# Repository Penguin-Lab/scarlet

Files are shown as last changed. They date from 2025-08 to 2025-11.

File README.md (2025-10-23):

# scarlet
A Scarlet é uma hexapod desenvolvida na disciplina de Robôs a Patas para andar de forma autônoma ou para ser controlada pelo celular. Para se locomover, ela possui 6 patas de 3 graus de liberdade cada (3 motores) e uma ESP32 que comanda o conjunto! Ela é a nossa viúva negra, a irmã da Tiffany e a nova integrante robótica do nosso espaço inteligente!

# Estrutura física
A estrutura física do robô é composta por seis patas de três eixos cada (três motores). As patas são fixadas a duas placas de PLA para deixar o robô firme. As peças são todas projetadas em 3D e foram impressas utilizando PLA, podendo ser encontradas na pasta Pecas_3d deste projeto.

   

## Peças 3D em STL
As peças em 3D desenvolvidas para este projeto foram baseadas no projeto da hexapod Tiffany. Na pasta Pecas_3d, estão listadas essas peças em STL. Para ajudar, segue abaixo uma lista de todas as peças que devem ser impressas e qual o valor da sua maior dimensão (para ajudar na escolha da impressora):
* Corpo
  * 1x [SCARLET_BODY_DOWN.STL (230 mm)](https://github.com/Penguin-Lab/scarlet/blob/main/Pecas_3d/SCARLET_BODY_DOWN.STL)
  * 1x [SCARLET_BODY_UP.STL (230 mm)](https://github.com/Penguin-Lab/scarlet/blob/main/Pecas_3d/SCARLET_BODY_UP.STL)
  * 4x [SCARLET_SPACER.STL (68 mm)](https://github.com/Penguin-Lab/scarlet/blob/main/Pecas_3d/SCARLET_SPACER.STL)
  * 2x [SCARLET_SPACER_FRONT.STL (68 mm)](https://github.com/Penguin-Lab/scarlet/blob/main/Pecas_3d/SCARLET_SPACER_FRONT.STL)
  * 1x [SCARLET_SUPPORT_PCI.STL (120 mm)](https://github.com/Penguin-Lab/scarlet/blob/main/Pecas_3d/SCARLET_SUPPORT_PCI.STL)
  * 1x [SCARLET_SUPPORT_SWITCH.STL (50 mm)](https://github.com/Penguin-Lab/scarlet/blob/main/Pecas_3d/SCARLET_SUPPORT_SWITCH.STL)
  * 1x [SCARLET_SYMBOL.STL (50 mm)](https://github.com/Penguin-Lab/scarlet/blob/main/Pecas_3d/SCARLET_SYMBOL.STL)
  * 1x [SCARLET_LOGO.STL (50 mm)](https://github.com/Penguin-Lab/scarlet/blob/main/Pecas_3d/SCARLET_LOGO.STL)
* Patas
  * 6x [SCARLET_TIBIA_LEFT.STL (141 mm)](https://github.com/Penguin-Lab/scarlet/blob/main/Pecas_3d/SCARLET_TIBIA_LEFT.STL)
  * 6x [SCARLET_TIBIA_LEFT.STL espelhado (141 mm)](https://github.com/Penguin-Lab/scarlet/blob/main/Pecas_3d/SCARLET_TIBIA_LEFT.STL)
  * 6x [SCARLET_TIBIA_MIDDLE.STL (63 mm)](https://github.com/Penguin-Lab/scarlet/blob/main/Pecas_3d/SCARLET_TIBIA_MIDDLE.STL)
  * 3x [SCARLET_SHIELD_A.STL (10 mm)](https://github.com/Penguin-Lab/scarlet/blob/main/Pecas_3d/SCARLET_SHIELD_A.STL)
  * 3x [SCARLET_SHIELD_A.STL espelhado (10 mm)](https://github.com/Penguin-Lab/scarlet/blob/main/Pecas_3d/SCARLET_SHIELD_A.STL)
  * 3x [SCARLET_SHIELD_B.STL (10 mm)](https://github.com/Penguin-Lab/scarlet/blob/main/Pecas_3d/SCARLET_SHIELD_B.STL)
  * 3x [SCARLET_SHIELD_B.STL espelhado (10 mm)](https://github.com/Penguin-Lab/scarlet/blob/main/Pecas_3d/SCARLET_SHIELD_B.STL)
  * 3x [SCARLET_FEMUR_FRONT.STL (110 mm)](https://github.com/Penguin-Lab/scarlet/blob/main/Pecas_3d/SCARLET_FEMUR_FRONT.STL)
  * 3x [SCARLET_FEMUR_BACK.STL (118 mm)](https://github.com/Penguin-Lab/scarlet/blob/main/Pecas_3d/SCARLET_FEMUR_BACK.STL)
  * 3x [SCARLET_FEMUR_FRONT.STL espelhado (110 mm)](https://github.com/Penguin-Lab/scarlet/blob/main/Pecas_3d/SCARLET_FEMUR_FRONT.STL)
  * 3x [SCARLET_FEMUR_BACK.STL espelhado (118 mm)](https://github.com/Penguin-Lab/scarlet/blob/main/Pecas_3d/SCARLET_FEMUR_BACK.STL)
  * 6x [SCARLET_FEMUR_MIDDLE.STL (51 mm)](https://github.com/Penguin-Lab/scarlet/blob/main/Pecas_3d/SCARLET_FEMUR_MIDDLE.STL)
  * 6x [SCARLET_OMBRO_UP.STL (61 mm)](https://github.com/Penguin-Lab/scarlet/blob/main/Pecas_3d/SCARLET_OMBRO_UP.STL)
  * 3x [SCARLET_OMBRO_DOWN_LEFT.STL (61 mm)](https://github.com/Penguin-Lab/scarlet/blob/main/Pecas_3d/SCARLET_OMBRO_DOWN_LEFT.STL)
  * 3x [SCARLET_OMBRO_DOWN_LEFT.STL espelhado (61 mm)](https://github.com/Penguin-Lab/scarlet/blob/main/Pecas_3d/SCARLET_OMBRO_DOWN_LEFT.STL)
* Motor
  * 12x [SCARLET_TAMPA_MOTOR_DS3230.STL (41 mm)](https://github.com/Penguin-Lab/scarlet/blob/main/Pecas_3d/SCARLET_TAMPA_MOTOR_DS3230.STL)

Obs 1: a tampa de 12 motores deverão ser trocadas pelas peças [SCARLET_TAMPA_MOTOR_DS3230.STL](https://github.com/Penguin-Lab/scarlet/blob/main/Pecas_3d/SCARLET_TAMPA_MOTOR_DS3230.STL) para que seja possível fixar os rolamentos nas patas. Serão utilizados 3 rolamentos por pata.

Obs 2: os motores ficam fixados nas peças por [discos metálicos pequenos padrão para eixos de servo](https://a.aliexpress.com/_mPHt3nf).



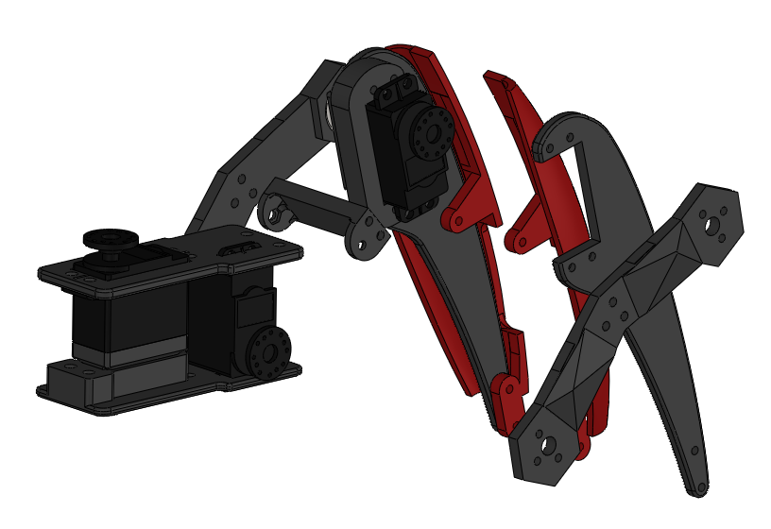
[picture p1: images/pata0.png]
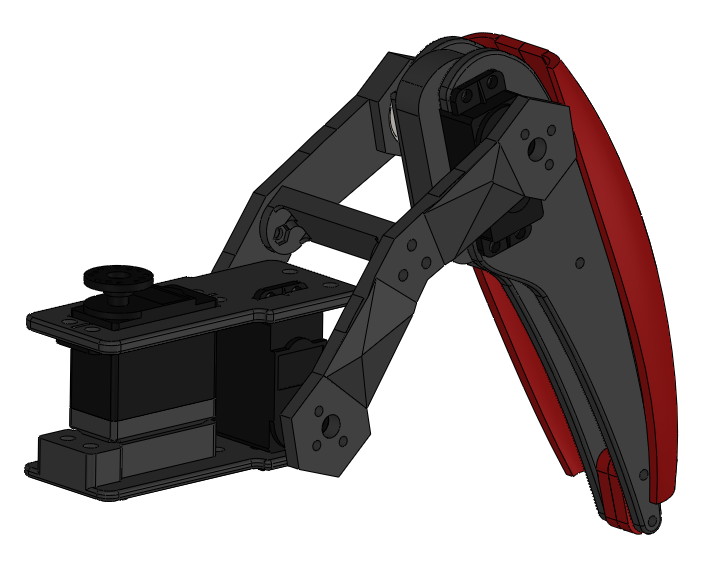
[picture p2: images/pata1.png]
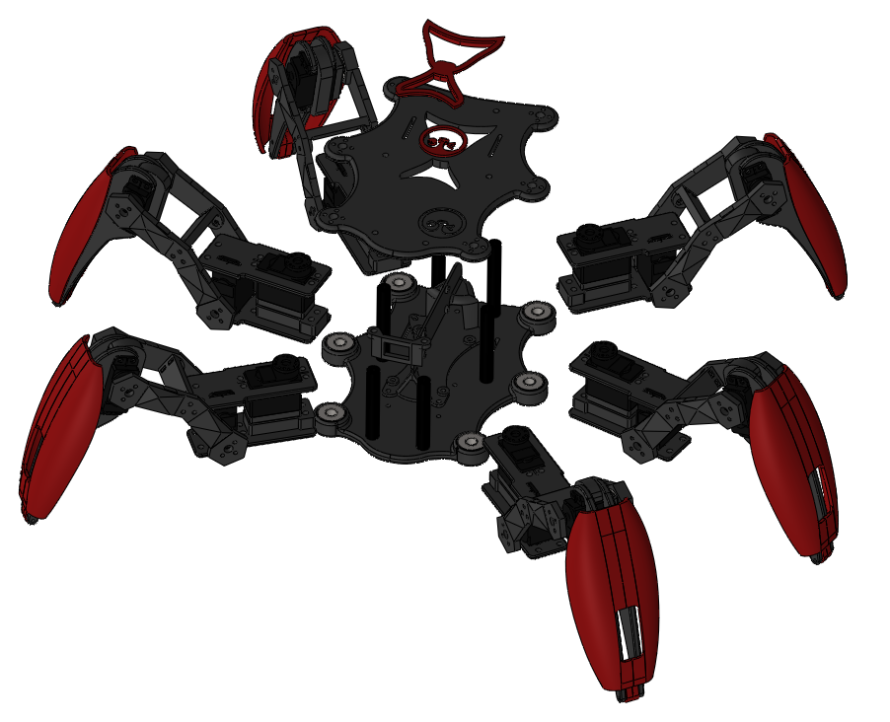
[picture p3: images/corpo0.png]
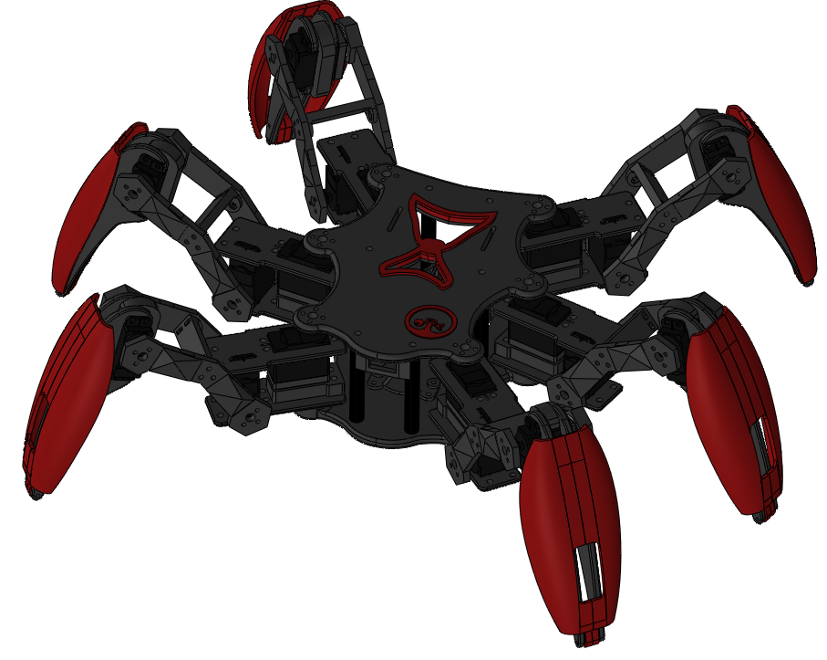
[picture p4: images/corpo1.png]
   

## Outros itens da estrutura
Alguns outros itens são necessários para finalizar a estrutura da Tiffany:
* 6x Parafusos m4 ou similar de cm, arruelas e porcas auto-travantes: prender as peças [SCARLET_BODY_UP.STL](https://github.com/Penguin-Lab/scarlet/blob/main/Pecas_3d/SCARLET_BODY_UP.STL) e [SCARLET_BODY_DOWN.STL](https://github.com/Penguin-Lab/scarlet/blob/main/Pecas_3d/SCARLET_BODY_DOWN.STL)
* 12x Parafusos m4 de 5 cm: prender as peças [SCARLET_OMBRO_DOWN_LEFT.STL](https://github.com/Penguin-Lab/scarlet/blob/main/Pecas_3d/SCARLET_OMBRO_DOWN_LEFT.STL) e [SCARLET_OMBRO_UP.STL](https://github.com/Penguin-Lab/scarlet/blob/main/Pecas_3d/SCARLET_OMBRO_UP.STL)
* 24x Parafusos m4 de 5,5 cm: prender as peças [SCARLET_OMBRO_DOWN_LEFT.STL](https://github.com/Penguin-Lab/scarlet/blob/main/Pecas_3d/SCARLET_OMBRO_DOWN_LEFT.STL) e [SCARLET_OMBRO_UP.STL](https://github.com/Penguin-Lab/scarlet/blob/main/Pecas_3d/SCARLET_OMBRO_UP.STL)
* Parafusos m3 de cm: prender todas as peças das patas e a [SCARLET_SUPORT_PCI.STL](https://github.com/Penguin-Lab/scarlet/blob/main/Pecas_3d/SCARLET_SUPORT_PCI.STL) no corpo do robô e na placa
* 6x Tiras de EVA de 5mm: colar e prender com braçadeira na ponta das peças [SCARLET_SHIELD_A.STL](https://github.com/Penguin-Lab/scarlet/blob/main/Pecas_3d/SCARLET_SHIELD_A.STL) e [SCARLET_SHIELD_B.STL](https://github.com/Penguin-Lab/scarlet/blob/main/Pecas_3d/SCARLET_SHIELD_B.STL) para evitar que o robô deslize

## Placa de circuito impresso
No projeto, foi desenvolvida uma placa de circuito para servir como shield para a ESP32 e conexão com as duas placas PCA9685 e com futuros sensores e displays I2C.

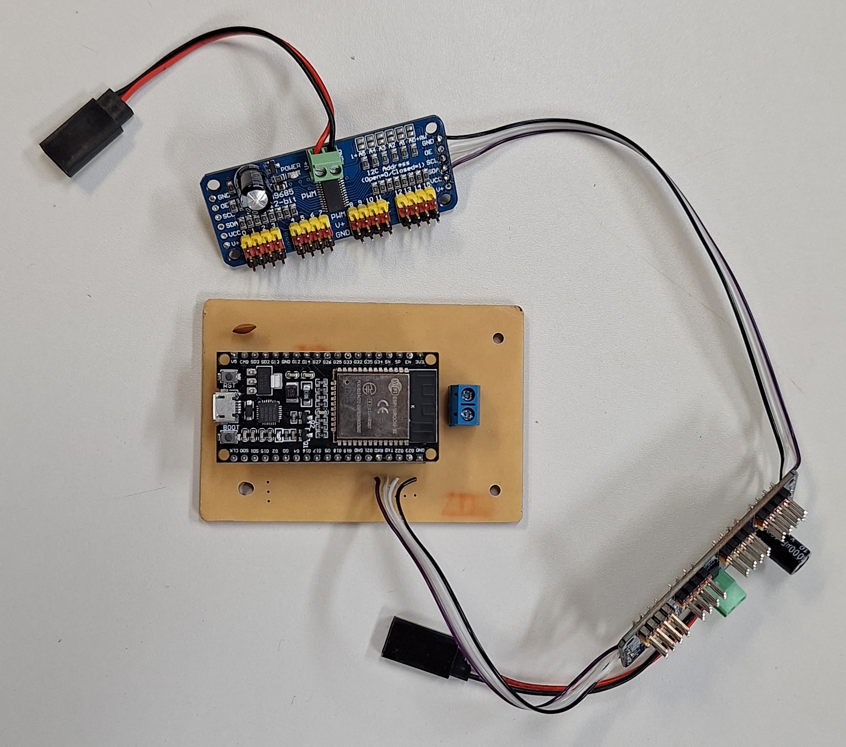
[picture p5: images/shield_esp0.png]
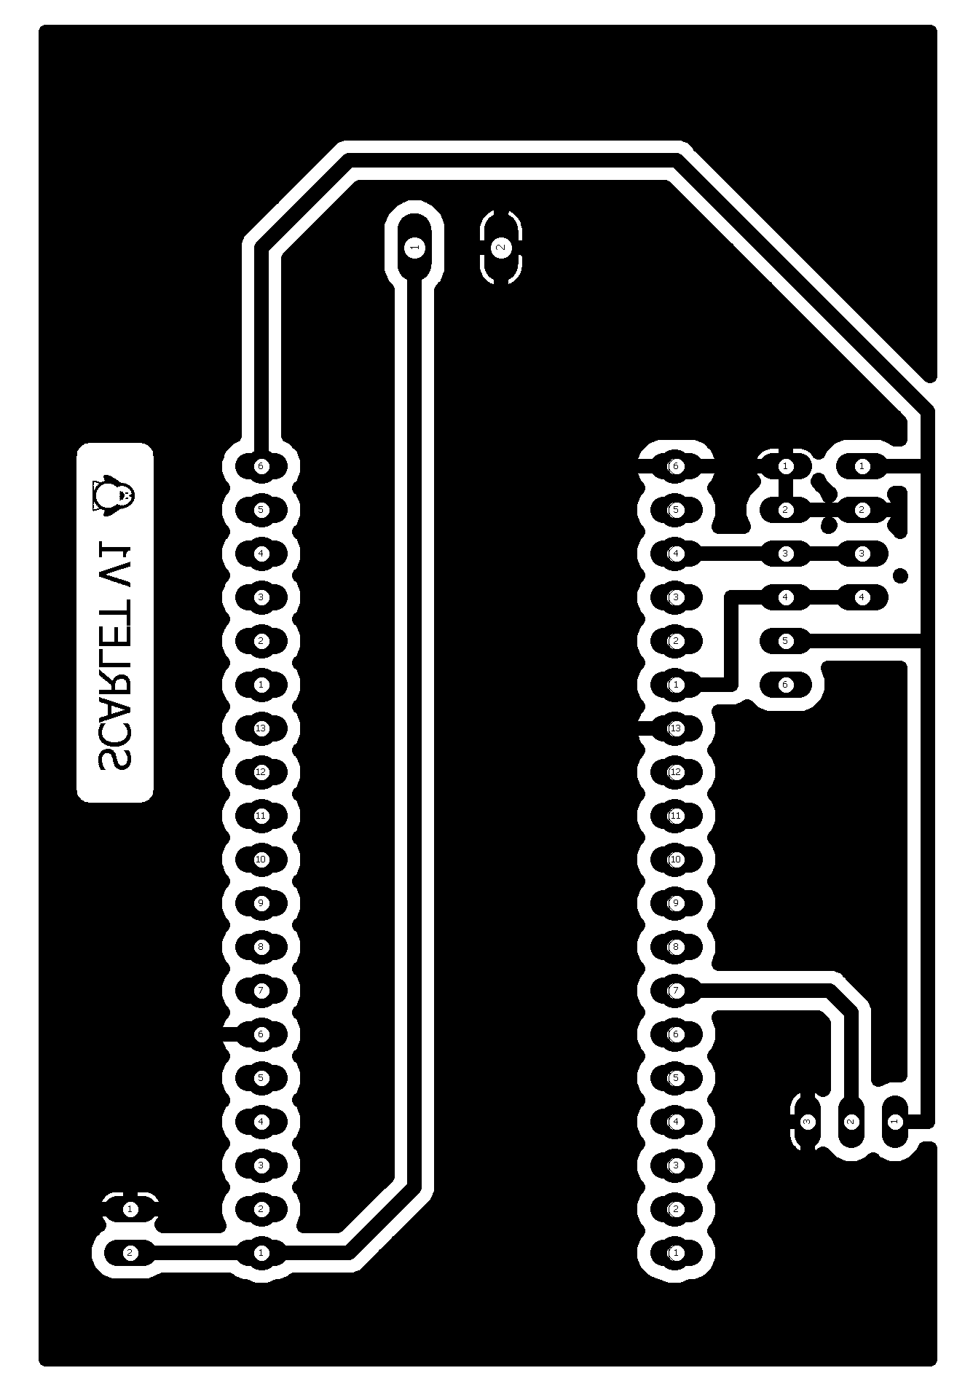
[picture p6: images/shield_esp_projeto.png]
    

## Calibração dos motores
A calibração dos motores é feita utilizando o [CALIBRADOR DE MOTORES](https://github.com/Penguin-Lab/calib_servomotor) conectado às PCAs da Scarlet. Isso deve ser feito pelo clock das PCAs ser diferente de uma placa para outra. Logo, os motores da esquerda são calibrados utilizando a PCA da esquerda e os da direita com a PCA da direita. Os valores retornados pela calibração são jogados nesta [PLANILHA](https://docs.google.com/spreadsheets/d/1Kh9AVbb79lXnJq5dlCiB7NEVVmcJWRX6X2CdDR9_QZo/edit?usp=sharing). A planilha ajeita os valores de PWM retornados na IDE do Arduino para valores que representem 0 e 180 graus dos motores já na estrutura das patas. Esses valores são os mesmos listados no código de comando da Scarlet.

## Componentes eletrônicos
Os componentes eletrônicos embarcados no robô e equipamentos utilizados são:
* Controlador com Wi-fi e Bluetooth
  * 1x ESP32 (38 pinos)
* Motores
  * 18x Servo DS3230 PRO-180
* 2x Placas PCA9685 para comando dos 18 motores
* Chave (switch)
* Alimentação
  * Bateria Zippy LiFe 1100mAh 2s 6,6V (ESP32)
  * Bateria TM Hobbies LiFe 2100mAh 2s 6,6v (motores)

# Software
Na pasta de códigos, há um código de programação da ESP32 (38 pinos). Ele é um exemplo em C++ do comando de movimentação da Tiffany:
* Dabble: a ESP32 pode se comunicar com o aplicativo Dabble no celular e receber comandos de ação.

## Alunos participantes e desenvolvedores da Scarlet
* Állefe Amorim Florindo
* Eduarda Ferreira Cipriano
* Gustavo Assis Ferreira
* Joab Felippe de Souza Lima
* João Pedro Queiroz dos Santos
* Junior Guimarães de Oliveira
* Luis Philipe Zioto de Barros
* Rafaela da Silva Crise
* Ricardo dos Santos Barros
* Samuel Gurgel Rocha

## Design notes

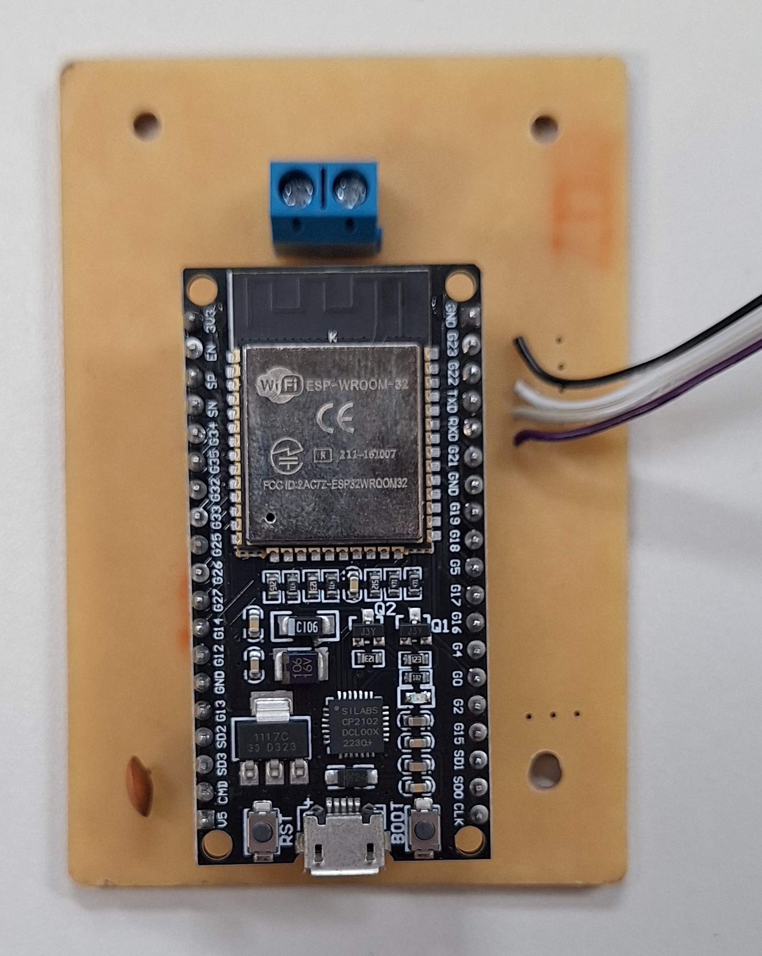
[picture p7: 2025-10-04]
images/shield_esp1.png

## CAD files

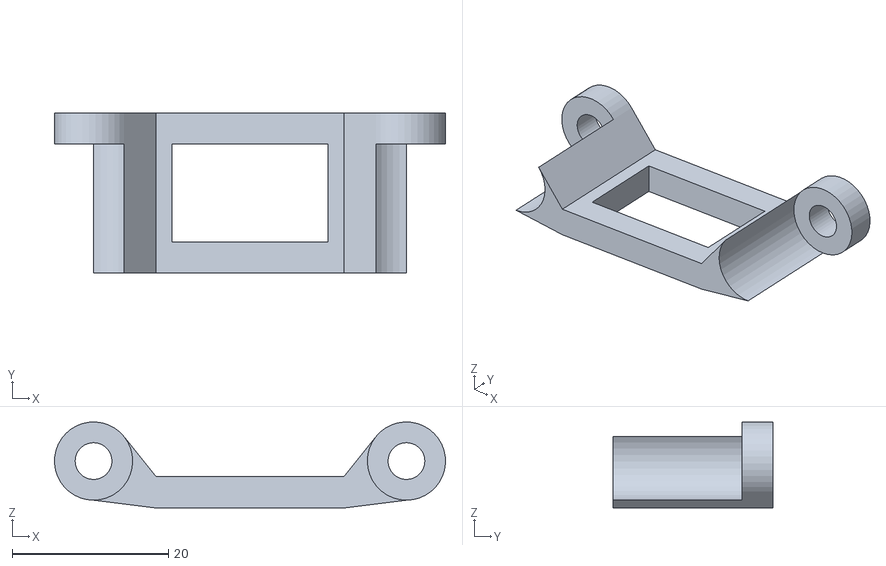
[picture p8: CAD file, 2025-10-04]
Pecas_3d/SCARLET_SUPORT_SWITCH.STL
50.0 x 20.5 x 11.0

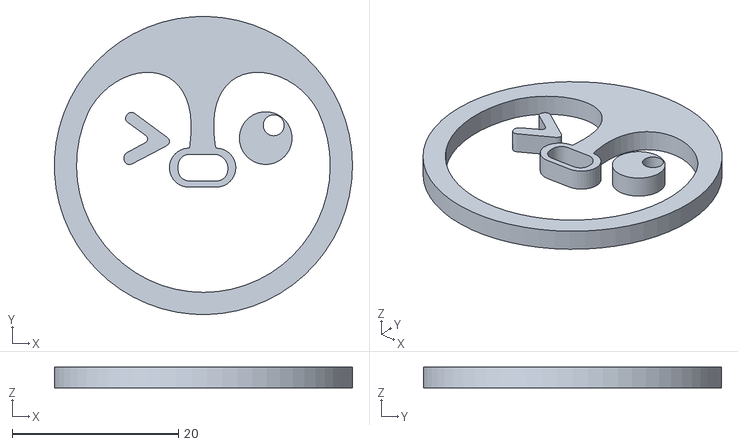
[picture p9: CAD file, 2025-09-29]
Pecas_3d/SCARLET_LOGO.STL
35.9 x 35.9 x 2.50

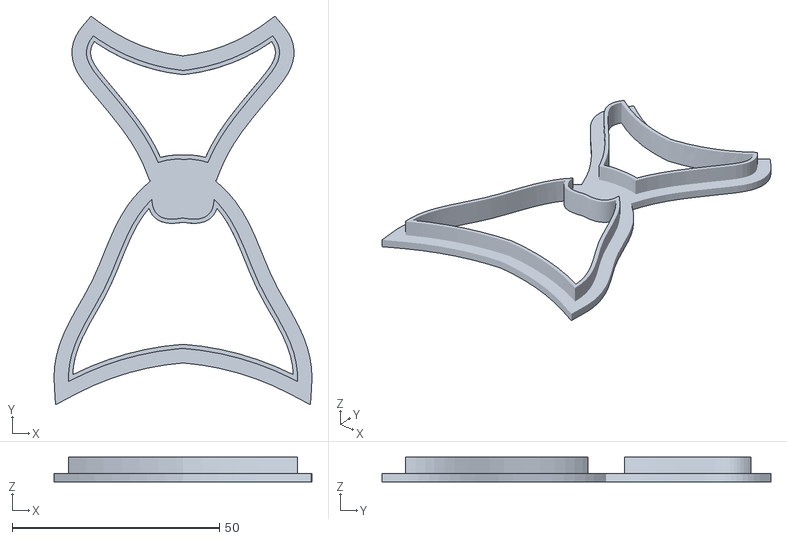
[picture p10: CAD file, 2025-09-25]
Pecas_3d/SCARLET_SYMBOL.STL
62.2 x 93.7 x 6.00

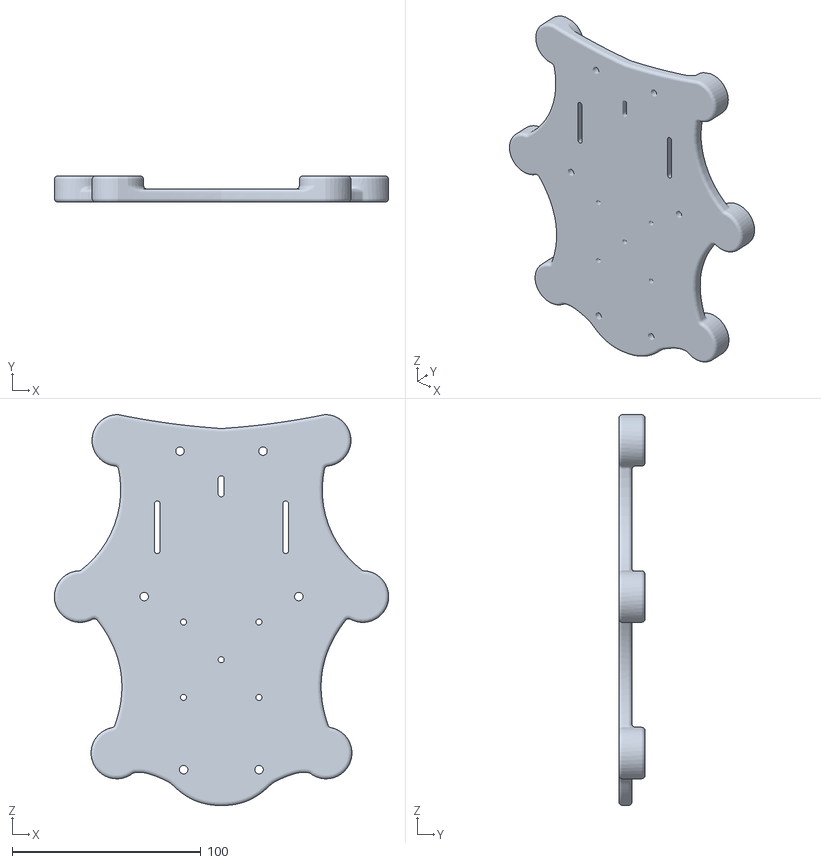
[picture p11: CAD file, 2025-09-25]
Pecas_3d/SCARLET_BODY_DOWN.STL
177.4 x 14.0 x 207.4

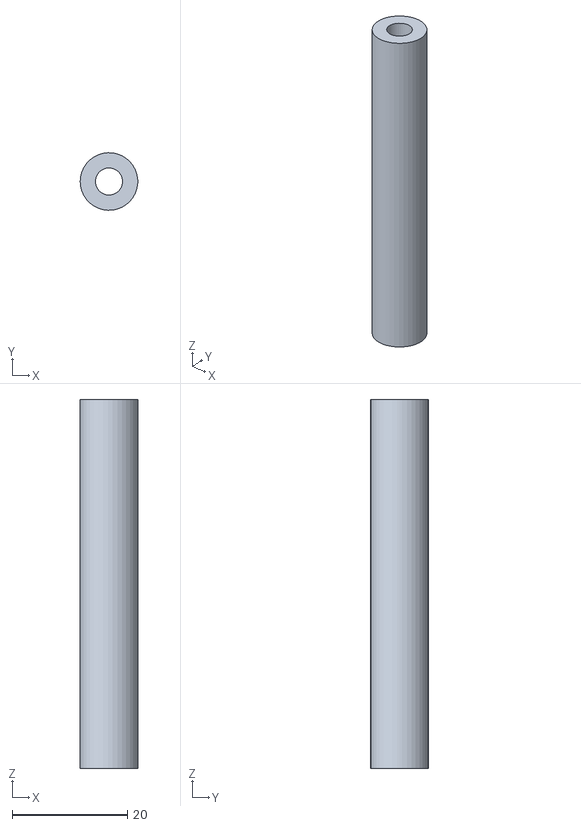
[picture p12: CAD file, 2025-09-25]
Pecas_3d/SCARLET_SPACER_FRONT.STL
10.0 x 9.99 x 64.0

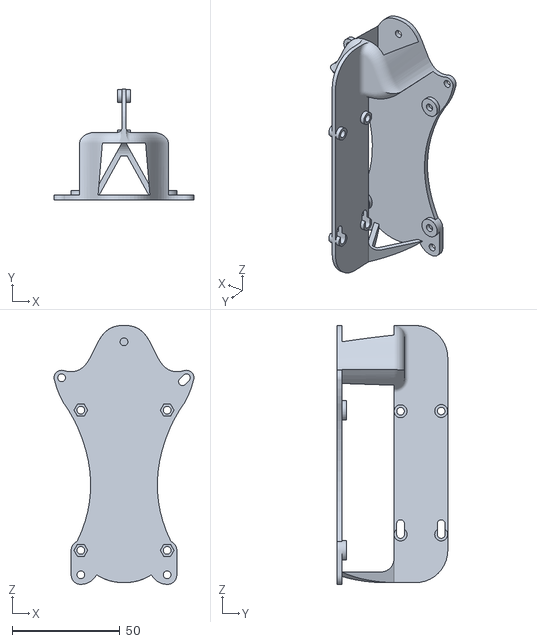
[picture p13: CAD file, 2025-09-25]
Pecas_3d/SCARLET_SUPORT_PCI.STL
64.8 x 51.3 x 120.1

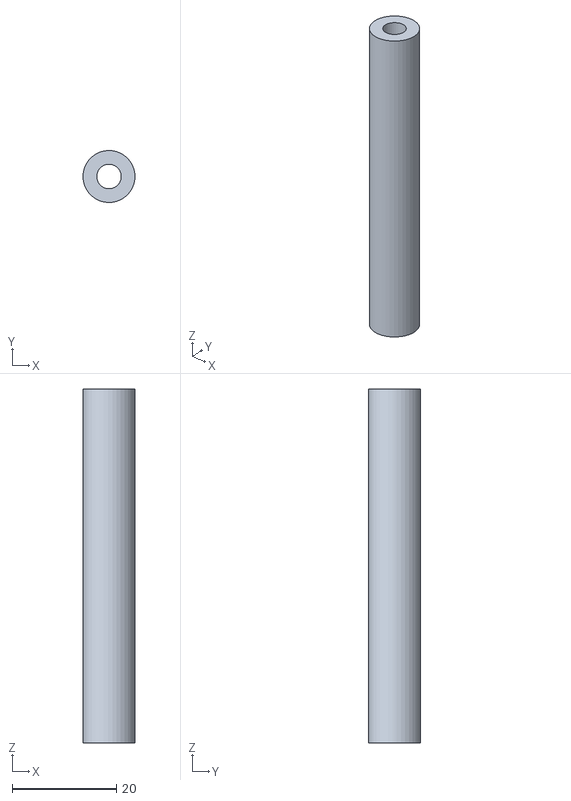
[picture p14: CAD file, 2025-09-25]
Pecas_3d/SCARLET_SPACER.STL
10.0 x 9.99 x 68.0

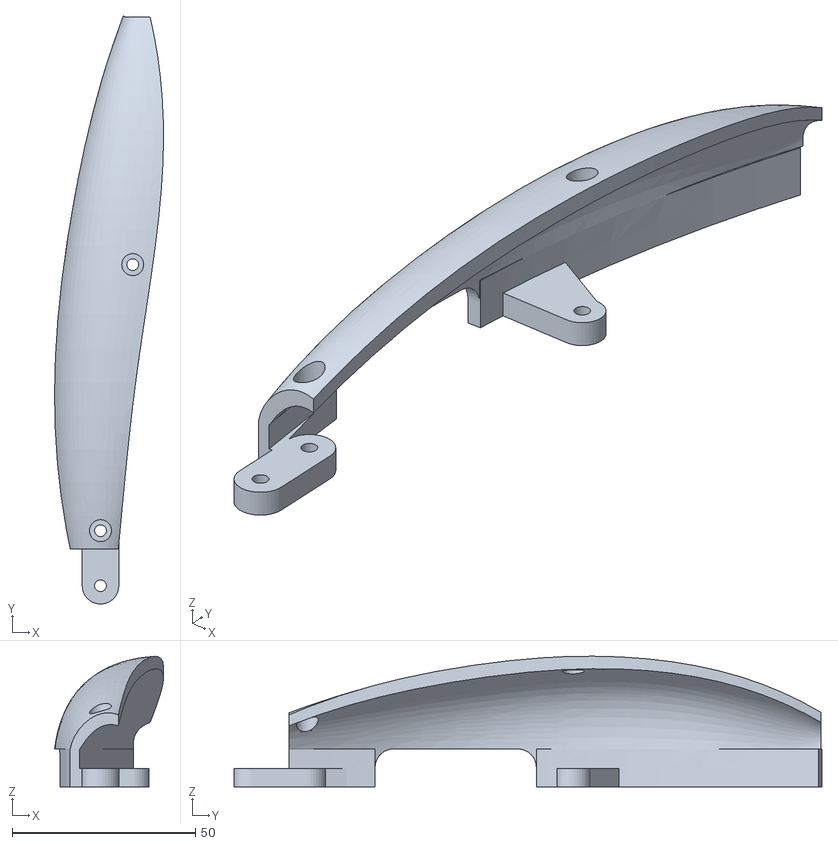
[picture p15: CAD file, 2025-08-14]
Pecas_3d/SCARLET_SHIELD_A.STL
29.7 x 160.2 x 35.6

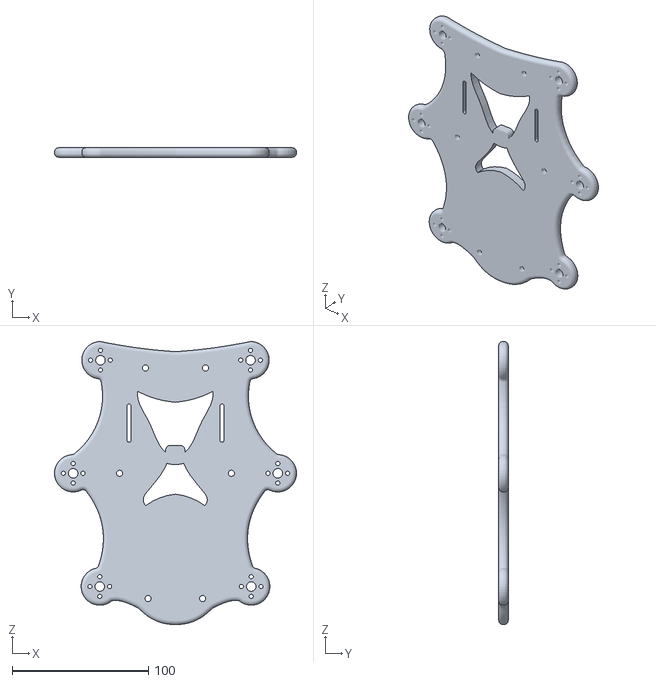
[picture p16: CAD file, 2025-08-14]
Pecas_3d/SCARLET_BODY_UP.STL
177.4 x 7.00 x 207.4

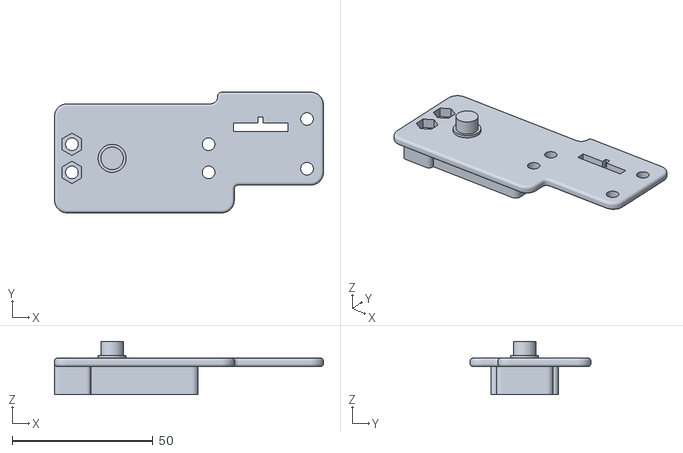
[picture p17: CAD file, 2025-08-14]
Pecas_3d/SCARLET_OMBRO_DOWN_LEFT.STL
95.7 x 43.0 x 19.0

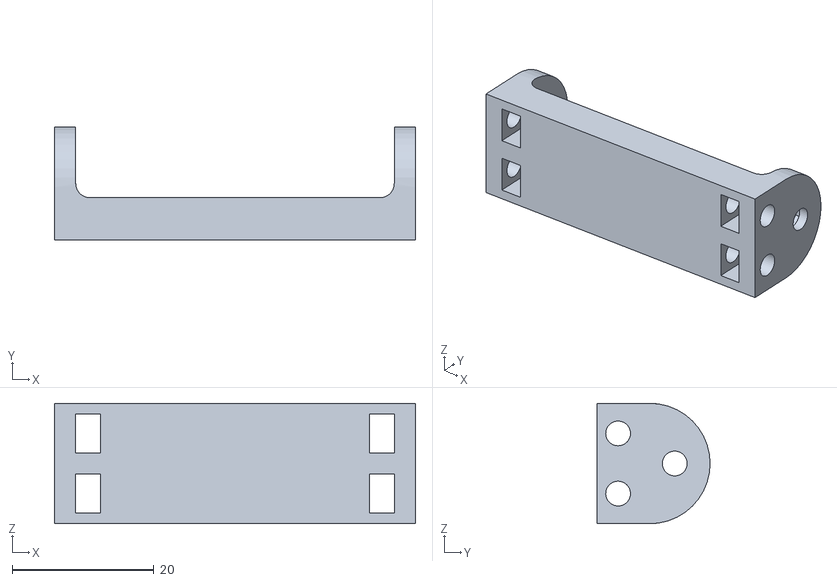
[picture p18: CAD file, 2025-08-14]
Pecas_3d/SCARLET_FEMUR_MIDDLE.STL
51.0 x 16.0 x 17.0

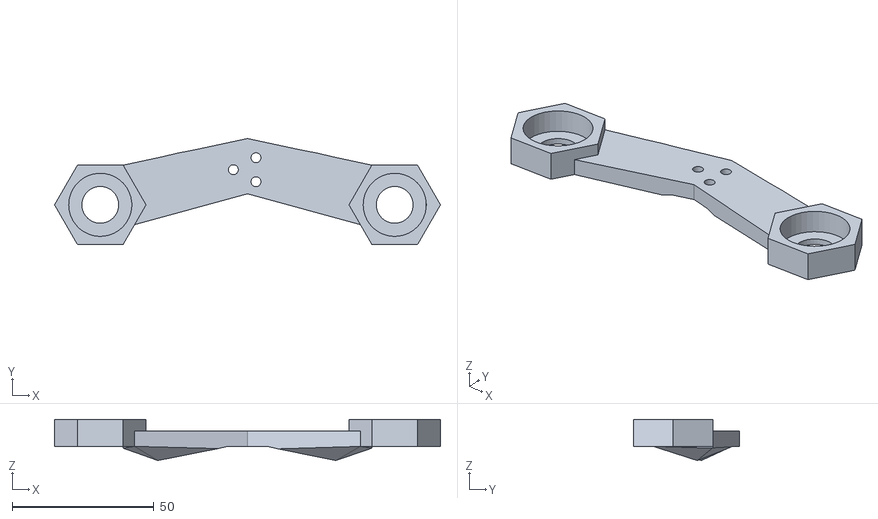
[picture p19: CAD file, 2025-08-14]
Pecas_3d/SCARLET_FEMUR_BACK.STL
136.3 x 37.4 x 14.5

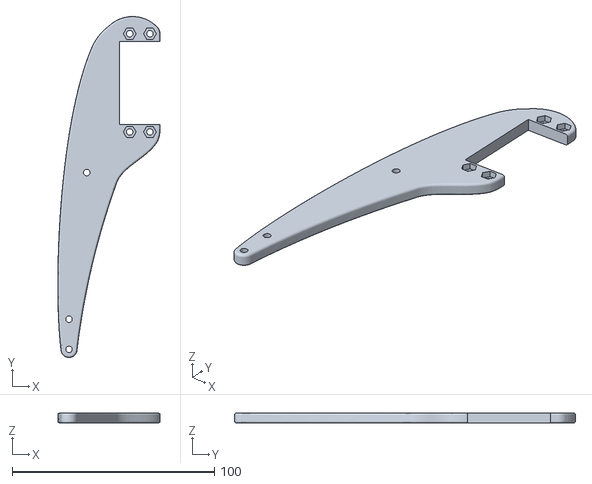
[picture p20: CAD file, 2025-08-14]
Pecas_3d/SCARLET_TIBIA_LEFT.STL
50.7 x 168.7 x 5.00

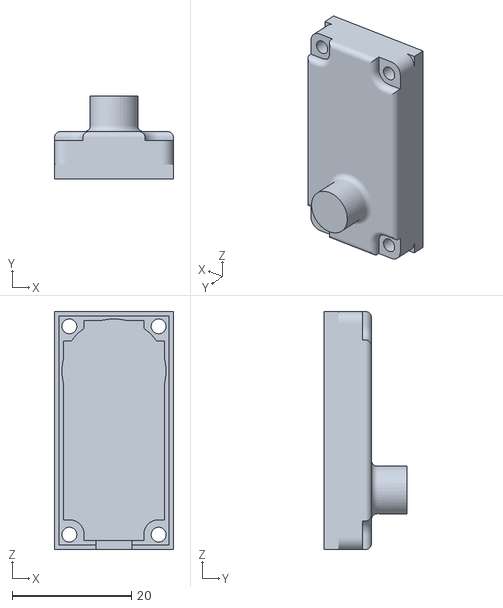
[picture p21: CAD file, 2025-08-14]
Pecas_3d/SCARLET_TAMPA_MOTOR_DS3230.STL
20.0 x 14.0 x 40.0

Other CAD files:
Pecas_3d/SCARLET_SHIELD_B.STL
Pecas_3d/SCARLET_FEMUR_FRONT.STL
Pecas_3d/SCARLET_OMBRO_UP.STL
Pecas_3d/SCARLET_TIBIA_MIDDLE.STL

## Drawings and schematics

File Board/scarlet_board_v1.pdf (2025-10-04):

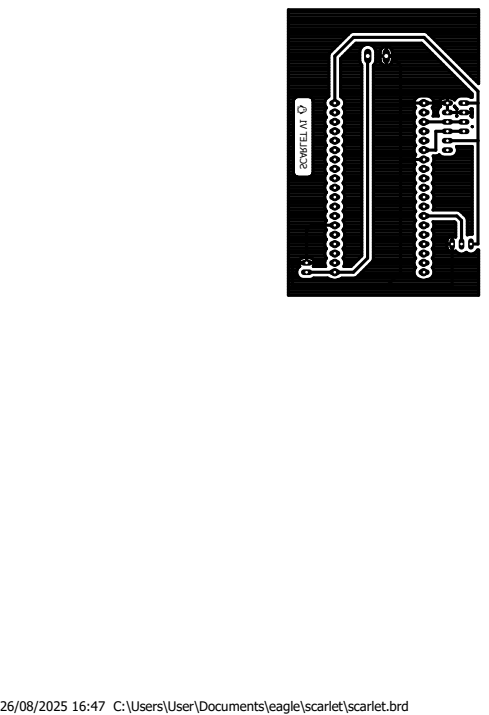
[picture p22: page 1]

26/08/2025 16:47 C:\Users\User\Documents\eagle\scarlet\scarlet.brd SCARLET V1

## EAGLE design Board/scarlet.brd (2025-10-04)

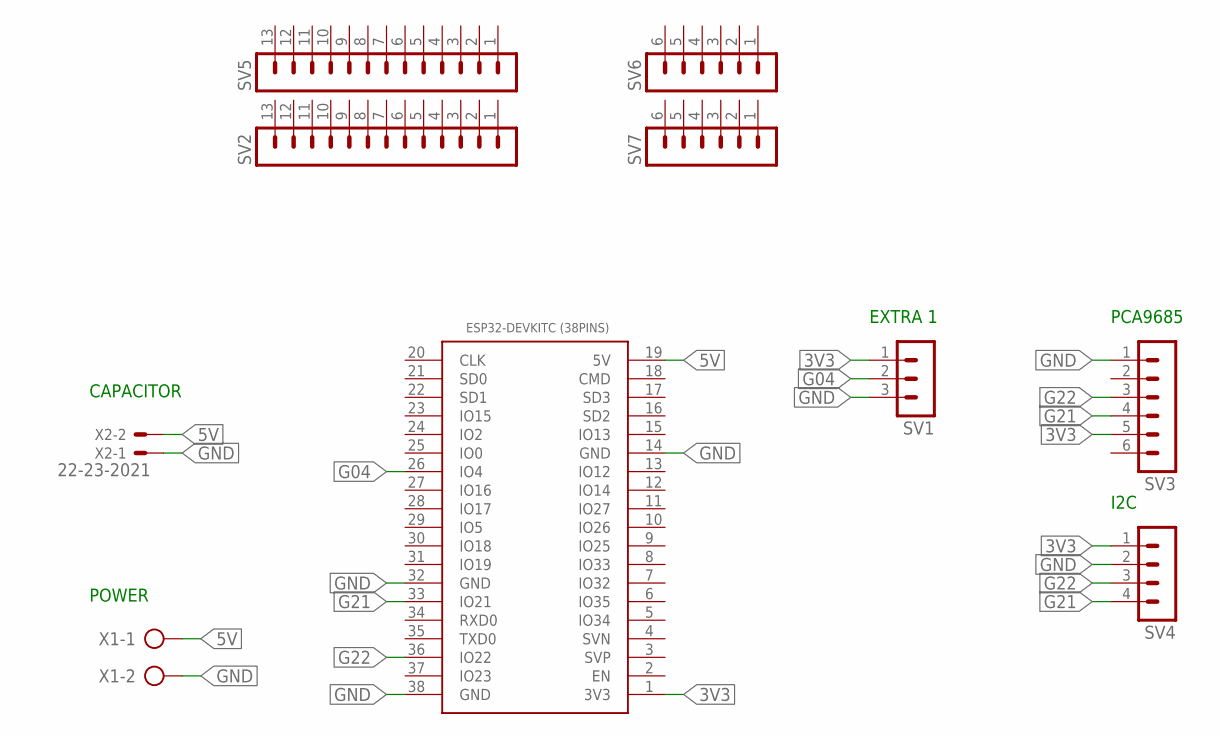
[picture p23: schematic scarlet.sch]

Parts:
ESP32-DEVKITC(38PINS)1: ESP32DEVKITC_38PINS; ESP32-DEVKITC
SV1: MA03-1
SV2, SV5: MA13-1
SV3, SV6, SV7: MA06-1
SV4: MA04-1
X1: AK300/2
X2: 22-23-2021

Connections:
3V3: ESP32-DEVKITC(38PINS)1.1 (3V3), SV1.1, SV3.5, SV4.1
5V: ESP32-DEVKITC(38PINS)1.19 (5V), X1.1, X2.2
G04: ESP32-DEVKITC(38PINS)1.26 (IO4), SV1.2
G21: ESP32-DEVKITC(38PINS)1.33 (IO21), SV3.4, SV4.4
G22: ESP32-DEVKITC(38PINS)1.36 (IO22), SV3.3, SV4.3
GND: ESP32-DEVKITC(38PINS)1.14 (GND), ESP32-DEVKITC(38PINS)1.32 (GND), ESP32-DEVKITC(38PINS)1.38 (GND), SV1.3, SV3.1, SV4.2, X1.2, X2.1

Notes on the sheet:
CAPACITOR
POWER
EXTRA 1
PCA9685
I2C

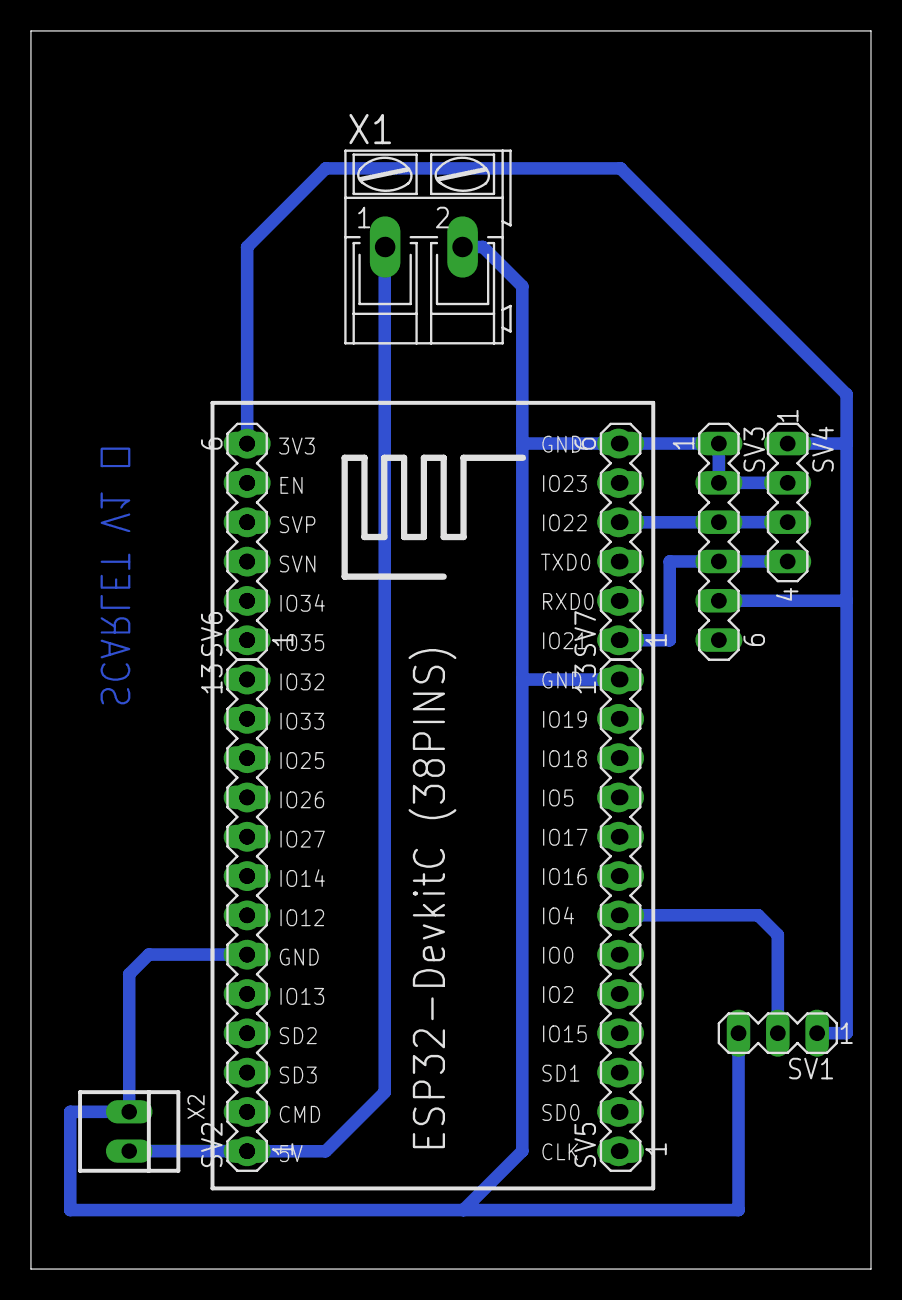
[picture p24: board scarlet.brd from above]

Board: 2 copper layers, 54.3 x 80.0 mm, 10 parts (0 on the bottom side), 6 nets.

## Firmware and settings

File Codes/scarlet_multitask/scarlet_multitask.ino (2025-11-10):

#define CUSTOM_SETTINGS
#define INCLUDE_GAMEPAD_MODULE
#include <DabbleESP32.h>
#include <Wire.h>
#include <Adafruit_PWMServoDriver.h>
#include <math.h>

#define TOTAL_PONTOS 25
#define METADE_PONTOS TOTAL_PONTOS / 2
#define TOTAL_PONTOS_CIRCULAR 25
#define DEBUG_SIMULADOR false

int OFFSET_ESQF = 0;
int OFFSET_DIRT = METADE_PONTOS;
int OFFSET_ESQM = METADE_PONTOS;
int OFFSET_DIRF = METADE_PONTOS;
int OFFSET_ESQT = 0;
int OFFSET_DIRM = 0;

Adafruit_PWMServoDriver pwmE = Adafruit_PWMServoDriver(0x40);
Adafruit_PWMServoDriver pwmD = Adafruit_PWMServoDriver(0x41);

struct int3 {
    int ombro, femur, tibia;

    // Soma
    int3 operator+(const int3& rhs) const {
      return { ombro + rhs.ombro, femur + rhs.femur, tibia + rhs.tibia };
    }

    // Subtracao
    int3 operator-(const int3& rhs) const {
      return { ombro - rhs.ombro, femur - rhs.femur, tibia - rhs.tibia };
    }

    // Multiplicacao por escalar
    int3 operator*(int scalar) const {
      return { ombro * scalar, femur * scalar, tibia * scalar };
    }

    // Divisao por escalar
    int3 operator/(int scalar) const {
      return { ombro / scalar, femur / scalar, tibia / scalar };
    }
};

struct float3 {
    float ombro, femur, tibia;

    // Soma
    float3 operator+(const float3& rhs) const {
      return { ombro + rhs.ombro, femur + rhs.femur, tibia + rhs.tibia };
    }

    // Subtracao
    float3 operator-(const float3& rhs) const {
      return { ombro - rhs.ombro, femur - rhs.femur, tibia - rhs.tibia };
    }

    // Multiplicacao por escalar
    float3 operator*(float scalar) const {
      return { ombro * scalar, femur * scalar, tibia * scalar };
    }

    // Divisao por escalar
    float3 operator/(float scalar) const {
      return { ombro / scalar, femur / scalar, tibia / scalar };
    }
};

int3 radToDegree(float3 angles_rad){
    return {int(angles_rad.ombro * 180.0 / M_PI),int(angles_rad.femur * 180.0 / M_PI),int(angles_rad.tibia * 180.0 / M_PI)};
}

float3 degreeToRad(int3 angles){
    return {float(angles.ombro) * M_PI / 180.0,float(angles.femur) * M_PI / 180.0,float(angles.tibia) * M_PI / 180.0};
}

struct floatxyz {
    float x, y, z;

    // Soma
    floatxyz operator+(const floatxyz& rhs) const {
      return { x + rhs.x, y + rhs.y, z + rhs.z };
    }

    // Subtracao
    floatxyz operator-(const floatxyz& rhs) const {
      return { x - rhs.x, y - rhs.y, z - rhs.z };
    }

    // Multiplicacao por escalar
    floatxyz operator*(float scalar) const {
      return { x * scalar, y * scalar, z * scalar };
    }

    // Divisao por escalar
    floatxyz operator/(float scalar) const {
      return { x / scalar, y / scalar, z / scalar };
    }

    floatxyz operator*(const floatxyz& rhs) const {
      return { x * rhs.x, y * rhs.y, z * rhs.z };
    }
};

float joystickToRad(int joystickAngle){
  float angle_rad = (float(joystickAngle)-90.0)*M_PI/180.0;
  while (angle_rad > M_PI) angle_rad -= 2*M_PI;
  while (angle_rad < -M_PI) angle_rad += 2*M_PI;
  
  return angle_rad;
}

int joystickToInt(int joystickAngle, int deltaAngle){
  int angle = joystickAngle-90;
  while (angle > 180) angle -= 360;
  while (angle < -180) angle += 360;
  // Verifica faixas e "trava" no valor mais proximo
  if (abs(angle - 180) <= deltaAngle || abs(angle + 180) <= deltaAngle){
    return 180;
  }
  else if (abs(angle - 90) <= deltaAngle){
    return 90;
  }
  else if (abs(angle + 90) <= deltaAngle){
    return -90;
  }
  else if (abs(angle) <= deltaAngle){
    return 0;
  }
  return angle;
}
struct Pata {
  Adafruit_PWMServoDriver* pwm;
  int3 pins;
  int3 angles;
  floatxyz xyz_ini;
  int3 LIMMIN;
  int3 LIMMAX;
  float L1, L2, L3;
  float P0[2], P1[2], P2[2], P3[2];

  Pata(Adafruit_PWMServoDriver* pwm, int pinOmbro, int pinFemur, int pinTibia, int OMIN, int OMAX, int FMIN, int FMAX, int TMIN, int TMAX) {
    this->pwm = pwm;
    this->pins = {pinOmbro,pinFemur,pinTibia};
    this->angles = {-1,-1,-1};
    this->xyz_ini = {0.0f,0.0f,0.0f};
    this->LIMMIN = {OMIN,FMIN,TMIN};
    this->LIMMAX = {OMAX,FMAX,TMAX};
    this->L1 = 5.28;
    this->L2 = 10.4;
    this->L3 = 14.62;
    this->P0[0] = 0.0;
    this->P0[1] = 0.0;
    this->P1[0] = 0.0;
    this->P1[1] = 0.0;
    this->P2[0] = 0.0;
    this->P2[1] = 0.0;
    this->P3[0] = 0.0;
    this->P3[1] = 0.0;
  }
  
  void moverPata(int angOmbro, int angFemur, int angTibia) {
    if (this->angles.ombro != angOmbro) {
      this->angles.ombro = angOmbro;
      int pulso = map(this->angles.ombro, 0, 180, LIMMIN.ombro, LIMMAX.ombro);
      pwm->setPWM(this->pins.ombro, 0, pulso);
    }
    if (this->angles.femur != angFemur) {
      this->angles.femur = angFemur;
      int pulso = map(this->angles.femur, 0, 180, LIMMIN.femur, LIMMAX.femur);
      pwm->setPWM(this->pins.femur, 0, pulso);
    }
    if (this->angles.tibia != angTibia) {
      this->angles.tibia = angTibia;
      int pulso = map(this->angles.tibia, 0, 180, LIMMIN.tibia, LIMMAX.tibia);
      pwm->setPWM(this->pins.tibia, 0, pulso);
    }
  }

  bool moverPataSuave(int angOmbro, int angFemur, int angTibia, int step) {
    bool stoped = true;
    if (this->angles.ombro != angOmbro) {
      stoped = false;
      if (abs(this->angles.ombro - angOmbro) < step){
        this->angles.ombro = angOmbro;
      }
      else{
        if (this->angles.ombro < angOmbro) this->angles.ombro += step;
        else this->angles.ombro -= step;
      }
      int pulso = map(this->angles.ombro, 0, 180, LIMMIN.ombro, LIMMAX.ombro);
      pwm->setPWM(this->pins.ombro, 0, pulso);
    }
    if (this->angles.femur != angFemur) {
      stoped = false;
      if (abs(this->angles.femur - angFemur) < step){
        this->angles.femur = angFemur;
      }
      else{
        if (this->angles.femur < angFemur) this->angles.femur += step;
        else this->angles.femur -= step;
      }
      int pulso = map(this->angles.femur, 0, 180, LIMMIN.femur, LIMMAX.femur);
      pwm->setPWM(this->pins.femur, 0, pulso);
    }
    if (this->angles.tibia != angTibia) {
      stoped = false;
      if (abs(this->angles.tibia - angTibia) < step){
        this->angles.tibia = angTibia;
      }
      else{
        if (this->angles.tibia < angTibia) this->angles.tibia += step;
        else this->angles.tibia -= step;
      }
      int pulso = map(this->angles.tibia, 0, 180, LIMMIN.tibia, LIMMAX.tibia);
      pwm->setPWM(this->pins.tibia, 0, pulso);
    }
    return stoped;
  }

  floatxyz cinematicaDireta(int3 angles){
    float3 angles_rad = degreeToRad(angles);
    floatxyz xyz;
																																																																																																  
    xyz.x = -sin(angles_rad.ombro)*(this->L1 + this->L3*cos(angles_rad.femur + angles_rad.tibia) + this->L2*cos(angles_rad.femur));
																																																																										 
    xyz.y = cos(angles_rad.ombro)*(this->L1 + this->L3*cos(angles_rad.femur + angles_rad.tibia) +this->L2*cos(angles_rad.femur));
    xyz.z = this->L3*sin(angles_rad.femur + angles_rad.tibia) + this->L2*sin(angles_rad.femur);
    return xyz;
  }

  int3 cinematicaInversa(floatxyz xyz){
    float3 angles_rad;
    float y_linha = sqrt(xyz.x * xyz.x + xyz.y * xyz.y) - this->L1;
    float L = sqrt(xyz.z * xyz.z + y_linha * y_linha);

    float alpha = acos(constrain((this->L2 * this->L2 + this->L3 * this->L3 - L * L) / (2 * this->L2 * this->L3), -1.0f, 1.0f));
    float beta = acos(constrain((L * L + this->L2 * this->L2 - this->L3 * this->L3) / (2 * L * this->L2), -1.0f, 1.0f));
    
    angles_rad.tibia = -M_PI + alpha;
    angles_rad.ombro = -atan2(xyz.x, xyz.y);
    angles_rad.femur = beta + atan2(xyz.z, y_linha);
    return radToDegree(angles_rad);
  }

  floatxyz trajetoriaLinear(floatxyz xyz_ini, int k, int offset, float angle_rad){
    floatxyz xyz;
    int kn = (k + offset) % TOTAL_PONTOS;
    if (kn < METADE_PONTOS){
      float t = float(kn)/(METADE_PONTOS-1);
      float u = 1 - t;
      xyz.x = xyz_ini.x + cos(angle_rad)*(-xyz_ini.x + u * u * u * this->P0[0] + 3 * u * u * t * this->P1[0] + 3 * u * t * t * this->P2[0] + t * t * t * this->P3[0]);
      xyz.y = xyz_ini.y + sin(angle_rad)*(-xyz_ini.x + u * u * u * this->P0[0] + 3 * u * u * t * this->P1[0] + 3 * u * t * t * this->P2[0] + t * t * t * this->P3[0]);
      xyz.z = u * u * u * this->P0[1] + 3 * u * u * t * this->P1[1] + 3 * u * t * t * this->P2[1] + t * t * t * this->P3[1];
    }
    else{
      xyz.x = xyz_ini.x + cos(angle_rad)*(-xyz_ini.x + this->P3[0] + (this->P0[0] - this->P3[0])*(float(kn - METADE_PONTOS) / (METADE_PONTOS - 1)));
      xyz.y = xyz_ini.y + sin(angle_rad)*(-xyz_ini.x + this->P3[0] + (this->P0[0] - this->P3[0])*(float(kn - METADE_PONTOS) / (METADE_PONTOS - 1)));
      xyz.z = xyz_ini.z;
    }
    return xyz;
  }

  floatxyz mapeiaTrajetoriaCircular(floatxyz xyz_ini, floatxyz xyz_atual, float step_length, float total_angle_rad, floatxyz Ombro){
    floatxyz xyz;
    // Mapeamento de trajetoria linear para curva (step_length = P3[0] - xyz_ini.x)
    float d_alpha = (total_angle_rad/2.0)*(xyz_atual.x - xyz_ini.x)/(step_length);
    // Translacao do ponto inicial da pata para as coordenadas do corpo
    float x = xyz_ini.x + Ombro.x;
    float y = xyz_ini.y + Ombro.y;
    float R = sqrt(x*x + y*y);
    float alpha = atan2(x,y);
    float n_alpha = alpha + d_alpha;
    xyz.x = R*sin(n_alpha) - Ombro.x;
    xyz.y = R*cos(n_alpha) - Ombro.y;
    xyz.z = xyz_atual.z;
    return xyz;
  }

  floatxyz trajetoriaPataBezier(floatxyz xyz_ini, int k, int offset, float dx, float dy, float dz, int totalPontos) {
    floatxyz xyz;
    int metadePontos = totalPontos/2;
    int kn = (k + offset) % totalPontos;
    float dx1 = dx/4.0;
    float dx2 = dx/2.0;
    float Px[4] = {xyz_ini.x, xyz_ini.x+dx1, xyz_ini.x+dx2, xyz_ini.x+dx};
    float dy1 = dy/4.0;
    float dy2 = dy/2.0;
    float Py[4] = {xyz_ini.y, xyz_ini.y+dy1, xyz_ini.y+dy2, xyz_ini.y+dy};
    float dz1 = dz/4.0;
    float dz2 = dz/2.0;
    float Pz[4] = {xyz_ini.z, xyz_ini.z+dz1+6.0, xyz_ini.z+dz2+10.0, xyz_ini.z+dz};
    if (kn < metadePontos){
      float t = float(kn)/(metadePontos-1);
      float u = 1 - t;
      xyz.x = u * u * u * Px[0] + 3 * u * u * t * Px[1] + 3 * u * t * t * Px[2] + t * t * t * Px[3];
      xyz.y = u * u * u * Py[0] + 3 * u * u * t * Py[1] + 3 * u * t * t * Py[2] + t * t * t * Py[3];
      xyz.z = u * u * u * Pz[0] + 3 * u * u * t * Pz[1] + 3 * u * t * t * Pz[2] + t * t * t * Pz[3];
    }
    else{
      xyz.x = Px[3];
      xyz.y = Py[3];
      xyz.z = Pz[3];
    }
    return xyz;
  }

  void atualizaBezier(float step_length){
    float half_stepping = step_length/2.0;
    this->P0[0] = this->xyz_ini.x - half_stepping;
    this->P0[1] = this->xyz_ini.z;
    this->P1[0] = this->P0[0] + half_stepping/2.0;
    this->P1[1] = this->P0[1] + 2.0*fabs(half_stepping);
    this->P3[0] = this->P0[0] + step_length;
    this->P3[1] = this->P0[1];
    this->P2[0] = this->P3[0] - half_stepping/2.0;
    this->P2[1] = this->P0[1] + fabs(2.0*half_stepping);
  }

  floatxyz iniciaPata(int3 anglesIni) {
    // Inicializa xyz inicial
    this->xyz_ini = this->cinematicaDireta(anglesIni);
    // Inicializa os vetores de trajetoria
    this->atualizaBezier(-8.0);
    // Move a pata para os angulos iniciais
    this->moverPata(anglesIni.ombro, anglesIni.femur, anglesIni.tibia);
    Serial.println("Perna iniciada!");
    return this->xyz_ini;
  }

  void escolheXyzini(int3 anglesIni){
    // Atualiza xyz inicial
    this->xyz_ini = this->cinematicaDireta(anglesIni);
    // Atualiza os vetores de trajetoria
    this->atualizaBezier(-8.0);
  }

  void moverPosIni() {
    int3 angles = cinematicaInversa(this->xyz_ini);
    // this->moverPata(angles.ombro, angles.femur, angles.tibia);
    this->moverPataSuave(angles.ombro, angles.femur, angles.tibia, 1);
  }
};

struct Hexapod {
  Pata &EsqF, &EsqM, &EsqT, &DirF, &DirM, &DirT;
  floatxyz OmbDirF, OmbDirM, OmbDirT, OmbEsqF, OmbEsqM, OmbEsqT; 

  Hexapod(Pata &EsqF, Pata &EsqM, Pata &EsqT, Pata &DirF, Pata &DirM, Pata &DirT):
    EsqF(EsqF), EsqM(EsqM), EsqT(EsqT), DirF(DirF), DirM(DirM), DirT(DirT) {
      OmbDirF = {8.30,-5.55,0.0};
      OmbDirM = {0.0,-7.50,0.0};
      OmbDirT = {-8.29,-5.50,0.0};
      OmbEsqF = {8.30,5.55,0.0};
      OmbEsqM = {0.0,7.50,0.0};
      OmbEsqT = {-8.29,5.50,0.0};
  }
  
  void ligarHexapod(){
    int totalPontos = 100;
    int metadePontos = totalPontos/2;
    int3 anglesF = {45,26,-100};
    int3 anglesM = {0,26,-100};
    int3 anglesT = {-45,26,-100};
    int3 anglesStartF = {anglesF.ombro,90,-145};
    int3 anglesStartM = {anglesM.ombro,90,-145};
    int3 anglesStartT = {anglesT.ombro,90,-145};
    // Manda a pata para a posicao inicial de coccum e guarda o xyz
    floatxyz xyzStartEsqF = this->EsqF.iniciaPata(anglesStartF);
    floatxyz xyzStartEsqM = this->EsqM.iniciaPata(anglesStartM);
    floatxyz xyzStartEsqT = this->EsqT.iniciaPata(anglesStartT);
    floatxyz xyzStartDirF = this->DirF.iniciaPata(anglesStartF);
    floatxyz xyzStartDirM = this->DirM.iniciaPata(anglesStartM);
    floatxyz xyzStartDirT = this->DirT.iniciaPata(anglesStartT);
    // Inicializa xyz_ini sem mover as patas
    this->EsqF.escolheXyzini(anglesF);
    this->EsqM.escolheXyzini(anglesM);
    this->EsqT.escolheXyzini(anglesT);
    this->DirF.escolheXyzini(anglesF);
    this->DirM.escolheXyzini(anglesM);
    this->DirT.escolheXyzini(anglesT);
    delay(1000);
    // Move as patas para (x_ini,y_ini,zStart)
    int k = 0;
    #if DEBUG_SIMULADOR
      this->enviarAngulos(k);
    #endif
    while (k < metadePontos){
      floatxyz xyzEsqF = this->EsqF.trajetoriaPataBezier(xyzStartEsqF, k, 0, EsqF.xyz_ini.x - xyzStartEsqF.x, EsqF.xyz_ini.y - xyzStartEsqF.y, 0, totalPontos);
      floatxyz xyzDirM = this->DirM.trajetoriaPataBezier(xyzStartDirM, k, 0, DirM.xyz_ini.x - xyzStartDirM.x, DirM.xyz_ini.y - xyzStartDirM.y, 0, totalPontos);
      floatxyz xyzEsqT = this->EsqT.trajetoriaPataBezier(xyzStartEsqT, k, 0, EsqT.xyz_ini.x - xyzStartEsqT.x, EsqT.xyz_ini.y - xyzStartEsqT.y, 0, totalPontos);
      floatxyz xyzDirF = this->DirF.trajetoriaPataBezier(xyzStartDirF, k, 0, DirF.xyz_ini.x - xyzStartDirF.x, DirF.xyz_ini.y - xyzStartDirF.y, 0, totalPontos);
      floatxyz xyzEsqM = this->EsqM.trajetoriaPataBezier(xyzStartEsqM, k, 0, EsqM.xyz_ini.x - xyzStartEsqM.x, EsqM.xyz_ini.y - xyzStartEsqM.y, 0, totalPontos);
      floatxyz xyzDirT = this->DirT.trajetoriaPataBezier(xyzStartDirT, k, 0, DirT.xyz_ini.x - xyzStartDirT.x, DirT.xyz_ini.y - xyzStartDirT.y, 0, totalPontos);
      int3 anglesEsqF = this->EsqF.cinematicaInversa(xyzEsqF);
      int3 anglesDirM = this->DirM.cinematicaInversa(xyzEsqM);
      int3 anglesEsqT = this->EsqT.cinematicaInversa(xyzEsqT);
      int3 anglesDirF = this->DirF.cinematicaInversa(xyzDirF);
      int3 anglesEsqM = this->EsqM.cinematicaInversa(xyzDirM);
      int3 anglesDirT = this->DirT.cinematicaInversa(xyzDirT);
      this->EsqF.moverPata(anglesEsqF.ombro, anglesEsqF.femur, anglesEsqF.tibia);
      this->DirM.moverPata(anglesDirM.ombro, anglesDirM.femur, anglesDirM.tibia);
      this->EsqT.moverPata(anglesEsqT.ombro, anglesEsqT.femur, anglesEsqT.tibia);
      this->DirF.moverPata(anglesDirF.ombro, anglesDirF.femur, anglesDirF.tibia);
      this->EsqM.moverPata(anglesEsqM.ombro, anglesEsqM.femur, anglesEsqM.tibia);
      this->DirT.moverPata(anglesDirT.ombro, anglesDirT.femur, anglesDirT.tibia);
      #if DEBUG_SIMULADOR
        this->enviarAngulos(k);
      #endif
      k++;
      delay(20);
    }
    delay(1000);
    // Atualiza a posicao inicial da pata para antes de descer para xyzini
    xyzStartEsqF = {this->EsqF.xyz_ini.x,this->EsqF.xyz_ini.y,xyzStartEsqF.z};
    xyzStartEsqM = {this->EsqM.xyz_ini.x,this->EsqM.xyz_ini.y,xyzStartEsqM.z};
    xyzStartEsqT = {this->EsqT.xyz_ini.x,this->EsqT.xyz_ini.y,xyzStartEsqT.z};
    xyzStartDirF = {this->DirF.xyz_ini.x,this->DirF.xyz_ini.y,xyzStartDirF.z};
    xyzStartDirM = {this->DirM.xyz_ini.x,this->DirM.xyz_ini.y,xyzStartDirM.z};
    xyzStartDirT = {this->DirT.xyz_ini.x,this->DirT.xyz_ini.y,xyzStartDirT.z};
    // Move as patas para (x_ini,y_ini,z_ini)
    k = 0;
    while (k < metadePontos){
      floatxyz xyzEsqF = this->EsqF.trajetoriaPataBezier(xyzStartEsqF, k, 0, 0, 0, EsqF.xyz_ini.z - xyzStartEsqF.z, totalPontos);
      floatxyz xyzDirM = this->DirM.trajetoriaPataBezier(xyzStartDirM, k, 0, 0, 0, DirM.xyz_ini.z - xyzStartDirM.z, totalPontos);
      floatxyz xyzEsqT = this->EsqT.trajetoriaPataBezier(xyzStartEsqT, k, 0, 0, 0, EsqT.xyz_ini.z - xyzStartEsqT.z, totalPontos);
      floatxyz xyzDirF = this->DirF.trajetoriaPataBezier(xyzStartDirF, k, 0, 0, 0, DirF.xyz_ini.z - xyzStartDirF.z, totalPontos);
      floatxyz xyzEsqM = this->EsqM.trajetoriaPataBezier(xyzStartEsqM, k, 0, 0, 0, EsqM.xyz_ini.z - xyzStartEsqM.z, totalPontos);
      floatxyz xyzDirT = this->DirT.trajetoriaPataBezier(xyzStartDirT, k, 0, 0, 0, DirT.xyz_ini.z - xyzStartDirT.z, totalPontos);
      int3 anglesEsqF = this->EsqF.cinematicaInversa(xyzEsqF);
      int3 anglesDirM = this->DirM.cinematicaInversa(xyzEsqM);
      int3 anglesEsqT = this->EsqT.cinematicaInversa(xyzEsqT);
      int3 anglesDirF = this->DirF.cinematicaInversa(xyzDirF);
      int3 anglesEsqM = this->EsqM.cinematicaInversa(xyzDirM);
      int3 anglesDirT = this->DirT.cinematicaInversa(xyzDirT);
      this->EsqF.moverPata(anglesEsqF.ombro, anglesEsqF.femur, anglesEsqF.tibia);
      this->DirM.moverPata(anglesDirM.ombro, anglesDirM.femur, anglesDirM.tibia);
      this->EsqT.moverPata(anglesEsqT.ombro, anglesEsqT.femur, anglesEsqT.tibia);
      this->DirF.moverPata(anglesDirF.ombro, anglesDirF.femur, anglesDirF.tibia);
      this->EsqM.moverPata(anglesEsqM.ombro, anglesEsqM.femur, anglesEsqM.tibia);
      this->DirT.moverPata(anglesDirT.ombro, anglesDirT.femur, anglesDirT.tibia);
      #if DEBUG_SIMULADOR
        this->enviarAngulos(k);
      #endif					 
      k++;
      delay(20);
    }
  }
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
void loop(){
}

int estado = 11;
int angle_joystick = 90;
int mode = 0; // 0 - Omnidirecional, 1 - Rotacional

void TaskHexapod(void *pvParameters) {
  int k = 0;
  int totalPontos = TOTAL_PONTOS;
  for (;;) {
    if(estado == 1){ // "Dar a patinha": move patinha para a posição X = [x_ini+10;y_ini;z_ini+10]
        totalPontos = 50;
        int3 angles = {-10,-10,0};
        // scarlet.darPatinha(k,totalPontos);
        scarlet.darPatinhaAlto(k,angles,totalPontos);
        #if DEBUG_SIMULADOR
			    scarlet.enviarAngulos(k);
		    #endif
        if (k < (totalPontos/2)){
          k++;
        }
        vTaskDelay(pdMS_TO_TICKS(2));
    }
    else if(estado == 2){ // Rebola
        // int3 angles = {20,0,0};
        int3 angles = scarlet.circularRollPitchYaw(k, 10);
        scarlet.cinematicaInversaCorpo(angles);
        #if DEBUG_SIMULADOR
          scarlet.enviarAngulos(k);
        #endif				 
        if (k == TOTAL_PONTOS_CIRCULAR - 1){
          k = 0;
        }
        else{
          k++;
        }
        vTaskDelay(pdMS_TO_TICKS(20));
    }
    else if(estado == 3){ // Andar omnidirecional ou rotacional
        float angle = joystickToInt(angle_joystick,20);
        if (mode == 0){
		  float angle_rad = angle*M_PI/180.0;
          k = scarlet.andar(k,angle_rad);
        }
        else{
          k = scarlet.andarCircular(k,angle);
        }
        #if DEBUG_SIMULADOR
          scarlet.enviarAngulos(k);
        #endif				 
        vTaskDelay(pdMS_TO_TICKS(20));
    }
    else if(estado == 9){ // Arma
        scarlet.ligarHexapod();
        estado = 0;
        vTaskDelay(pdMS_TO_TICKS(500));
    }
    else if(estado == 10){ // Desarma
        scarlet.desligarHexapod();
        estado = 11;
        vTaskDelay(pdMS_TO_TICKS(1));
    }
    else if(estado == 0){
      k = 0;
      scarlet.parar();
      #if DEBUG_SIMULADOR
        scarlet.enviarAngulos(k);
      #endif	   
      vTaskDelay(pdMS_TO_TICKS(15));
    }
    else{
      vTaskDelay(pdMS_TO_TICKS(10));
    }
  }
}

void TaskComunicacao(void *pvParameters) {
  for (;;) {
    Dabble.processInput();
    if (estado != 11){
      if (GamePad.isRightPressed()||GamePad.isLeftPressed()){       // Modo rotacional
        mode = 1;
      }
      if (GamePad.isUpPressed()||GamePad.isDownPressed()){       // Modo omnidirecional
        mode = 0;
      }
      if (GamePad.isCirclePressed()){       // "Dar a patinha"
        estado = 1;
      }
      else if(GamePad.isTrianglePressed()){ // Rebola
        estado = 2;
      }
      else if(GamePad.getRadius() > 2){     // Andar omnidirecional
        angle_joystick = GamePad.getAngle();
        estado = 3;
      }
      else if(GamePad.isSelectPressed()){   // Desarma
        estado = 10;
      }
      else{
        estado = 0;
      }
    }
    else{
      if(GamePad.isStartPressed()){         // Arma
        estado = 9;
      }
    }
    vTaskDelay(pdMS_TO_TICKS(20));   
  }
}

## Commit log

2025-10-20 corrigido o calculo de P0, P1, P2 e P3
    [scarlet_multitask.ino]
2025-10-23 Disable debug mode and adjust calibration values
2025-10-23 Add motor calibration section to README
    Added motor calibration section with details and links.
2025-10-30 Refactor trajectory calculations and update calibration
    Removed QUARTO_PONTOS definition and adjusted calculations in trajetoriaLinear function. Updated Pata DirT calibration values.
